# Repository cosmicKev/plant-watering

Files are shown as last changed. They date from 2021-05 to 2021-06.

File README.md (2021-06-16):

# Self Watering Plant

To keep your veggies alive that came alive from the [OfferZen] (http://offerzen.com/nl/make) workshop

# Features
  - ESP32 (Wifi / Bluetooth)
  - Flashing is done with a single USB-TypeC
  - Power in:
    - USB at 5V @ 2A max
  - Outputs
    - 2x waterpumps individually with shared power supply of either +5V or +12V
    - 2x USB 5V led strips individually controlled.
  - Sensors:
    - 2x external moisture sensors
    - 1x on board light sensor
    - 1x on board humidity & temperature sesor
    - 1x user custom sensor (till 3.3V

# MCAD - Mechanical CAD
## Pot pipe clips

## Electronics Enclosure

# ECAD - Electronics CAD

# Firmware

# Version

# Authors
Kevin Pinto

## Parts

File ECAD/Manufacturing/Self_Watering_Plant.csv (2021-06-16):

Comment | Designator | Footprint | LCSC Part #
10nF Unpolarized capacitor, small symbol | C1,C3,C11,C13 | C_0603_1608Metric
10uF Unpolarized capacitor, small symbol | C2 | C_0603_1608Metric
0.1uF Unpolarized capacitor, small symbol | C4,C5,C7,C8,C15,C16,C17 | C_0603_1608Metric
1uF Unpolarized capacitor, small symbol | C6,C12,C14 | C_0603_1608Metric
NCD0603R1 Light emitting diode | D1,D2,D4,D5,D7,D8 | LED_0603_1608Metric
RS3ABG Diode | D3,D6 | D_SMB
Polyfuse_Small Resettable fuse, polymeric positive temperature coefficient, small symbol | F1 | Fuse_1812_4532Metric
Conn_01x02 Generic connector, single row, 01x02, script generated (kicad-library-utils/schlib/autogen/connector/) | J1,J2 | TB001-500-02BE
USB_A USB Type A connector | J3,J6 | USB_A_Molex_67643_Horizontal
Conn_01x02 Generic connector, single row, 01x02, script generated (kicad-library-utils/schlib/autogen/connector/) | J7,J8 | JST_XH_S2B-XH-A_1x02_P2.50mm_Horizontal
Conn_01x03 Generic connector, single row, 01x03, script generated (kicad-library-utils/schlib/autogen/connector/) | J9 | JST_XH_S3B-XH-A_1x03_P2.50mm_Horizontal
C-31-M-12 USB 2.0-only Type-C Plug connector | P1 | USB_C_Receptacle_HRO_TYPE-C-31-M-12
BC817 0.8A Ic, 45V Vce, NPN Transistor, SOT-23 | Q1,Q2 | SOT-23
TEPT4400 Ambient Light Sensor, NPN Epitaxial Planar Phototransistor, T-1 | Q9 | LED_D3.0mm_Clear
10K Resistor, small symbol | R1,R4,R8,R9,R11,R14 | R_0603_1608Metric
5.1K Resistor, small symbol | R2,R5,R13,R15 | R_0603_1608Metric
1K Resistor, small symbol | R3,R6,R7,R12,R17,R18 | R_0603_1608Metric
0 Resistor, small symbol | R10 | R_0603_1608Metric
SW_Push Push button switch, generic, two pins | SW1 | SW_PUSH_6mm_H4.3mm
ESP32-WROOM-32 RF Module, ESP32-D0WDQ6 SoC, Wi-Fi 802.11b/g/n, Bluetooth, BLE, 32-bit, 2.7-3.6V, onboard antenna, SMD | U1 | ESP32-WROOM-32
NCE3018AS VDS =30V,ID =18A RDS(ON) < 7mΩ @ VGS=10V RDS(ON) < 10mΩ @ VGS=4.5V | U2,U9,U13,U14 | SO-8_3.9x4.9mm_P1.27mm
CH340C USB serial converter, UART, SOIC-16 | U3 | SOIC-16_3.9x9.9mm_P1.27mm
AHT20 | U4 | SOIC-6
NC7SB3157P6X Single SPDT Low-Voltage Analog Switch or 2:1 Multiplexer/De-Multiplexer Bus Switch, 10Ohm Ron, SC-70-6 | U5,U6,U7 | SOT-363_SC-70-6
BCT2028 | U11 | SOT-23-5

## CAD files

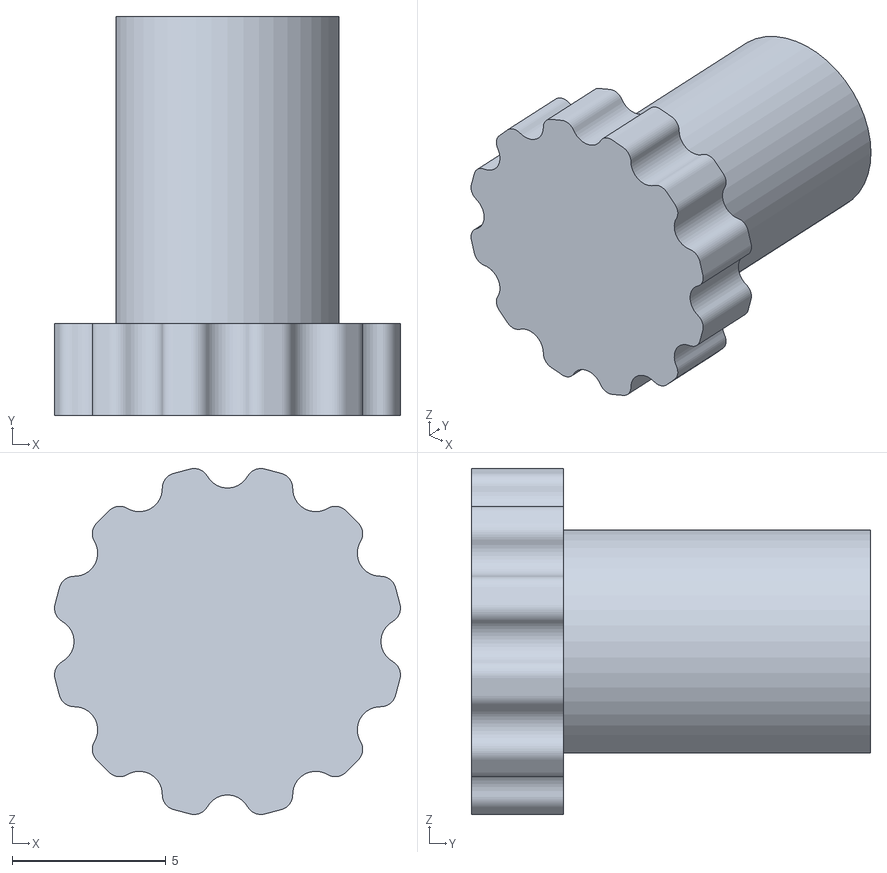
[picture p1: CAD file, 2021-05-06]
MCAD/PipeCork.STL
11.3 x 13.0 x 11.3

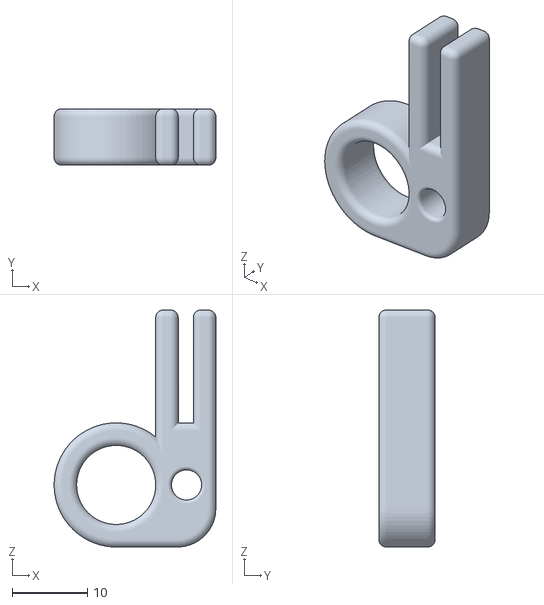
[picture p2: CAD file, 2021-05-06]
MCAD/PipeClip.STL
21.5 x 7.50 x 31.5

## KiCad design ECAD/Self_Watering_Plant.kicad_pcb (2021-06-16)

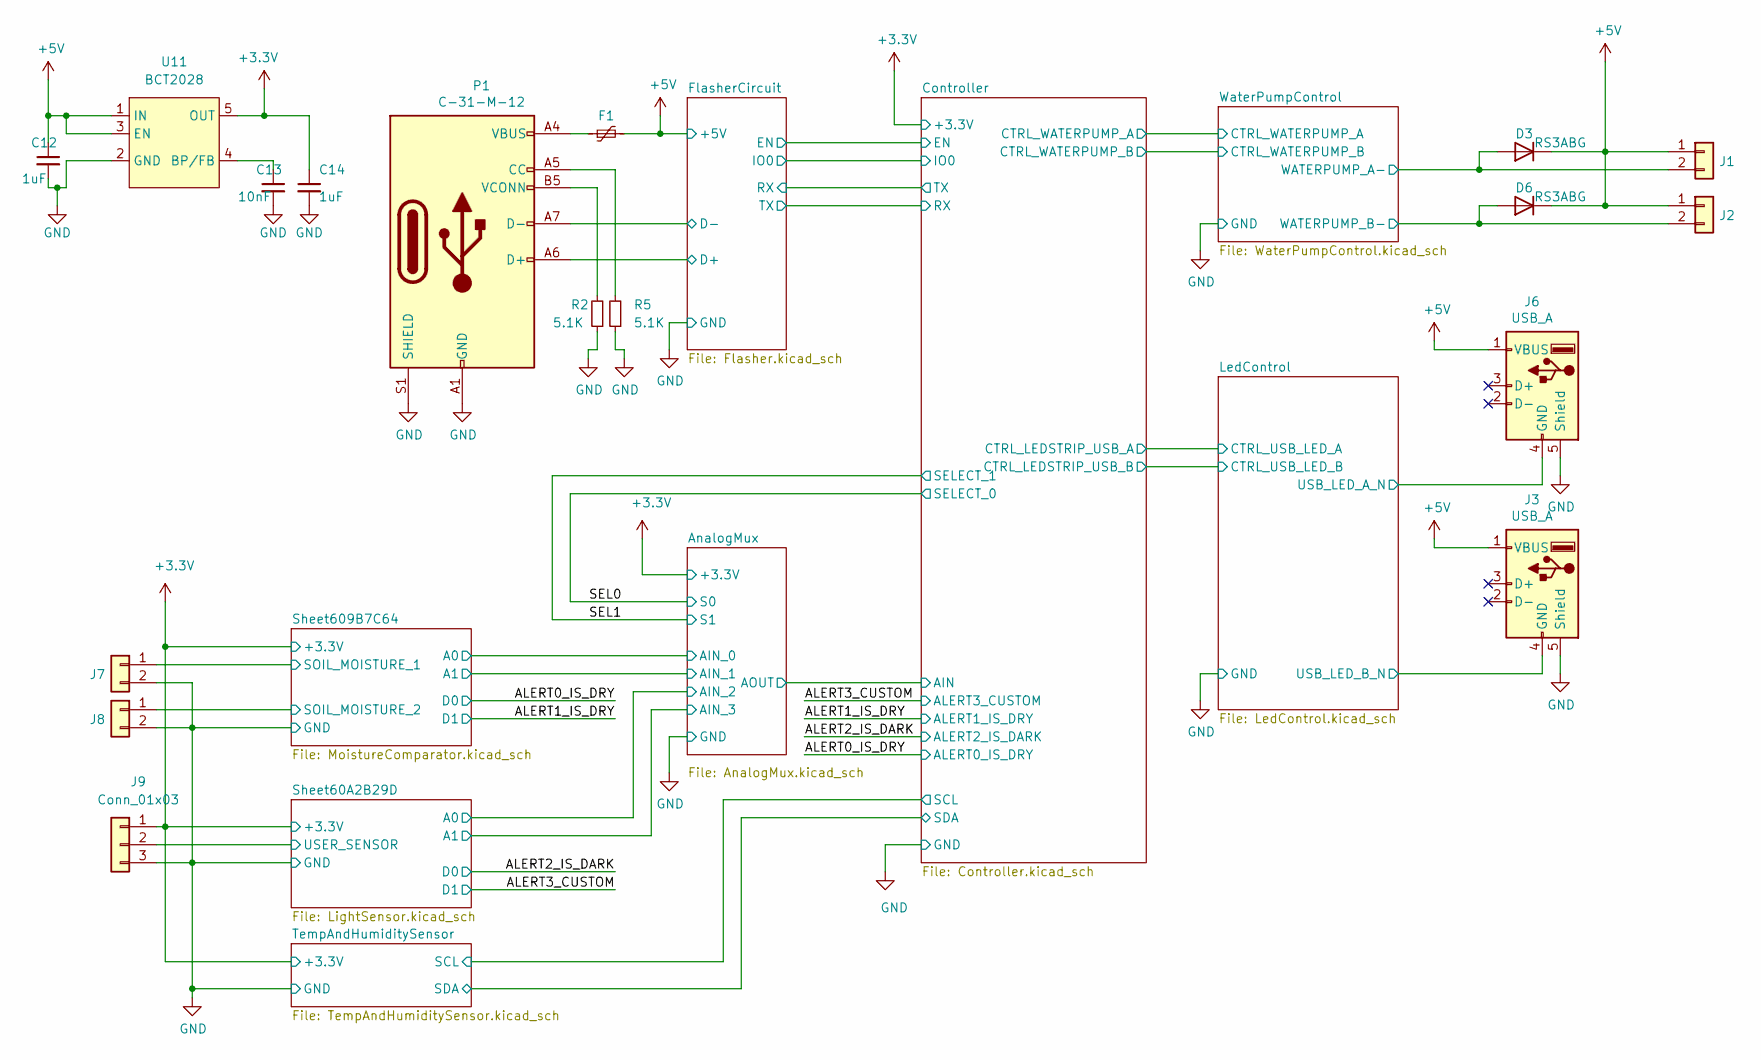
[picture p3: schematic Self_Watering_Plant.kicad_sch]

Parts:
C12, C14: 1uF; C_0603_1608Metric
C13: 10nF; C_0603_1608Metric
D3, D6: RS3ABG; D_SMB
F1: Polyfuse_Small; Fuse_1812_4532Metric
J1, J2: Conn_01x02; TB001-500-02BE
J3, J6: USB_A; USB_A_Molex_67643_Horizontal
J7, J8: Conn_01x02; JST_XH_S2B-XH-A_1x02_P2.50mm_Horizontal
J9: Conn_01x03; JST_XH_S3B-XH-A_1x03_P2.50mm_Horizontal
P1: C-31-M-12; USB_C_Receptacle_HRO_TYPE-C-31-M-12
R2, R5: 5.1K; R_0603_1608Metric
U11: BCT2028; SOT-23-5

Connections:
+3V3: C14.1, J9.1, U11.5 (OUT); also elsewhere on the board
+5V: C12.1, D3.1 (K), D6.1 (K), F1.2, J1.1, J2.1, J3.1 (VBUS), J6.1 (VBUS), U11.1 (IN), U11.3 (EN); also elsewhere on the board
/AnalogMux/AIN_0: J8.1; also elsewhere on the board
/AnalogMux/AIN_1: J7.1; also elsewhere on the board
/AnalogMux/AIN_2: J9.2; also elsewhere on the board
/FlasherCircuit/D+: P1.A6 (D+); also elsewhere on the board
/FlasherCircuit/D-: P1.A7 (D-); also elsewhere on the board
/LedControl/USB_LED_A_N: J6.4 (GND); also elsewhere on the board
/LedControl/USB_LED_B_N: J3.4 (GND); also elsewhere on the board
/WaterPumpControl/WATERPUMP_A-: D3.2 (A), J1.2; also elsewhere on the board
/WaterPumpControl/WATERPUMP_B-: D6.2 (A), J2.2; also elsewhere on the board
GND: C12.2, C13.2, C14.2, J3.5 (Shield), J6.5 (Shield), J7.2, J8.2, J9.3, P1.A1 (GND), P1.A12 (GND), P1.B1 (GND), P1.B12 (GND), P1.S1 (SHIELD), R2.1, R5.1, U11.2 (GND); also elsewhere on the board
unnamed: C13.1, U11.4 (BP/FB)
unnamed: F1.1, P1.A4 (VBUS), P1.A9 (VBUS), P1.B4 (VBUS), P1.B9 (VBUS)
unnamed: P1.A5 (CC), R5.2
unnamed: P1.B5 (VCONN), R2.2

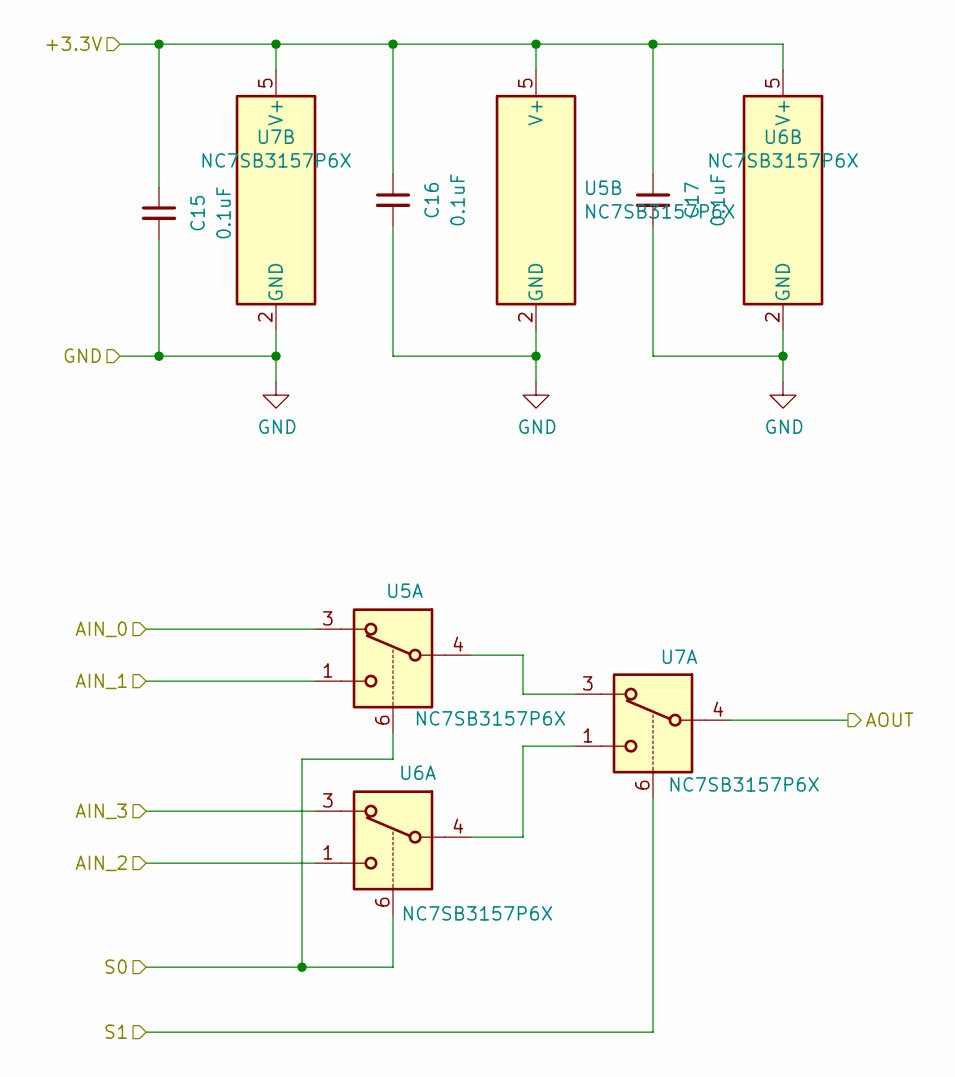
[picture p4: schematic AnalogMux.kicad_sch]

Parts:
C15, C16, C17: 0.1uF; C_0603_1608Metric
U5, U6, U7: NC7SB3157P6X; SOT-363_SC-70-6

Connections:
+3V3: C15.1, C16.1, C17.1, U5.5 (V+), U6.5 (V+), U7.5 (V+); also elsewhere on the board
/AnalogMux/AIN_0: U5.3; also elsewhere on the board
/AnalogMux/AIN_1: U5.1; also elsewhere on the board
/AnalogMux/AIN_2: U6.1; also elsewhere on the board
/AnalogMux/AIN_3: U6.3; also elsewhere on the board
/AnalogMux/AOUT: U7.4; also elsewhere on the board
/SEL0: U5.6, U6.6; also elsewhere on the board
/SEL1: U7.6; also elsewhere on the board
GND: C15.2, C16.2, C17.2, U5.2 (GND), U6.2 (GND), U7.2 (GND); also elsewhere on the board
unnamed: U5.4, U7.3
unnamed: U6.4, U7.1

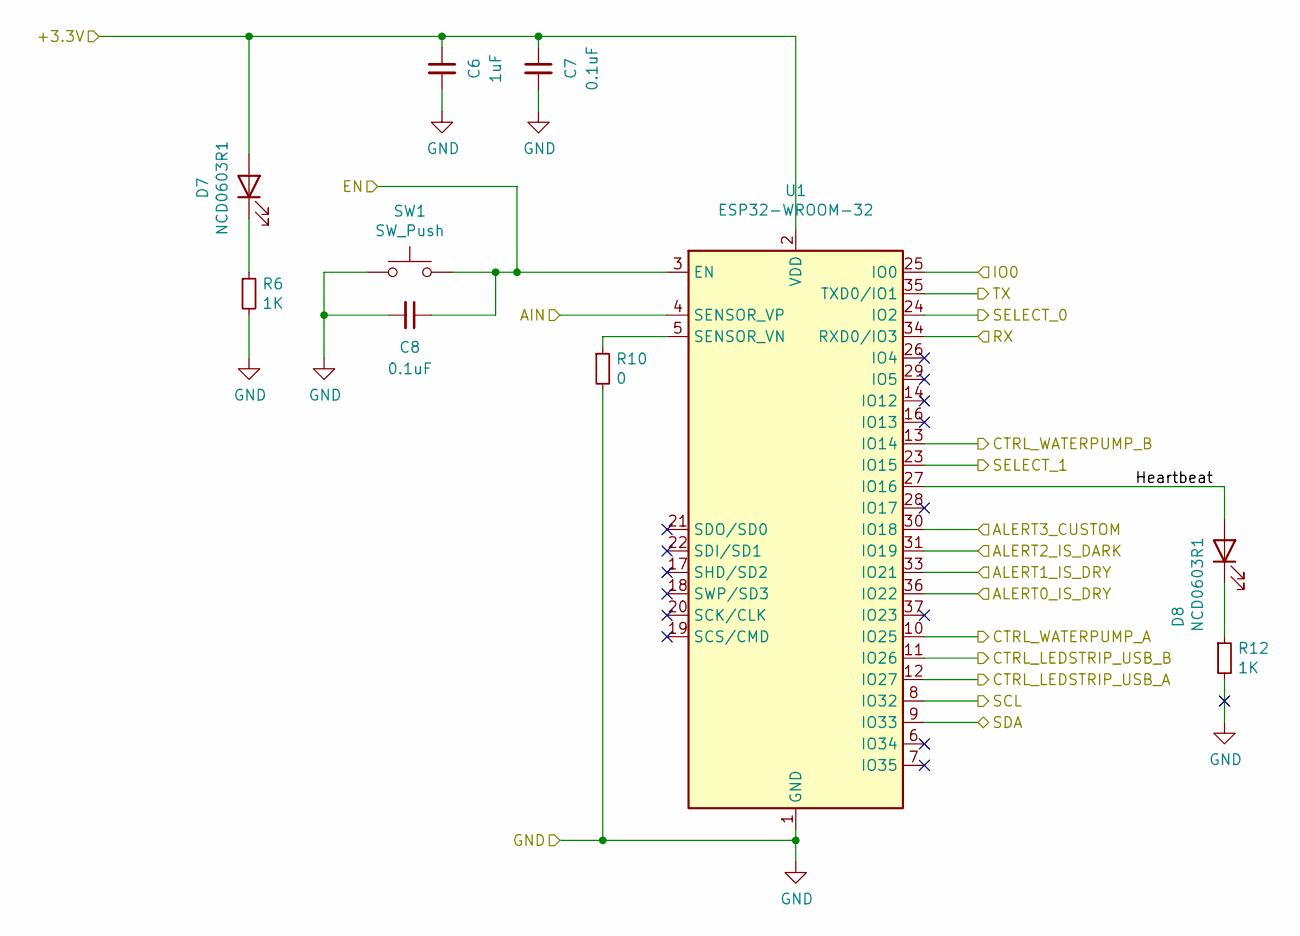
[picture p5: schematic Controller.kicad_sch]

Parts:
C6: 1uF; C_0603_1608Metric
C7, C8: 0.1uF; C_0603_1608Metric
D7, D8: NCD0603R1; LED_0603_1608Metric
R6, R12: 1K; R_0603_1608Metric
R10: 0; R_0603_1608Metric
SW1: SW_Push; SW_PUSH_6mm_H4.3mm
U1: ESP32-WROOM-32

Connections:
+3V3: C6.1, C7.1, D7.2 (A), U1.2 (VDD); also elsewhere on the board
/ALERT0_IS_DRY: U1.36 (IO22); also elsewhere on the board
/ALERT1_IS_DRY: U1.33 (IO21); also elsewhere on the board
/ALERT2_IS_DARK: U1.31 (IO19); also elsewhere on the board
/ALERT3_CUSTOM: U1.30 (IO18); also elsewhere on the board
/AnalogMux/AOUT: U1.4 (SENSOR_VP); also elsewhere on the board
/Controller/CTRL_LEDSTRIP_USB_A: U1.12 (IO27); also elsewhere on the board
/Controller/CTRL_LEDSTRIP_USB_B: U1.11 (IO26); also elsewhere on the board
/Controller/CTRL_WATERPUMP_A: U1.10 (IO25); also elsewhere on the board
/Controller/CTRL_WATERPUMP_B: U1.13 (IO14); also elsewhere on the board
/Controller/EN: C8.1, SW1.2, U1.3 (EN); also elsewhere on the board
/Controller/Heartbeat: D8.2 (A), U1.27 (IO16)
/Controller/IO0: U1.25 (IO0); also elsewhere on the board
/Controller/RX: U1.34 (RXD0/IO3); also elsewhere on the board
/Controller/SCL: U1.8 (IO32); also elsewhere on the board
/Controller/SDA: U1.9 (IO33); also elsewhere on the board
/Controller/TX: U1.35 (TXD0/IO1); also elsewhere on the board
/SEL0: U1.24 (IO2); also elsewhere on the board
/SEL1: U1.23 (IO15); also elsewhere on the board
GND: C6.2, C7.2, C8.2, R6.2, R10.2, R12.2, SW1.1, U1.1 (GND), U1.15 (GND), U1.38 (GND), U1.39 (GND); also elsewhere on the board
unnamed: D7.1 (K), R6.1
unnamed: D8.1 (K), R12.1
unnamed: R10.1, U1.5 (SENSOR_VN)

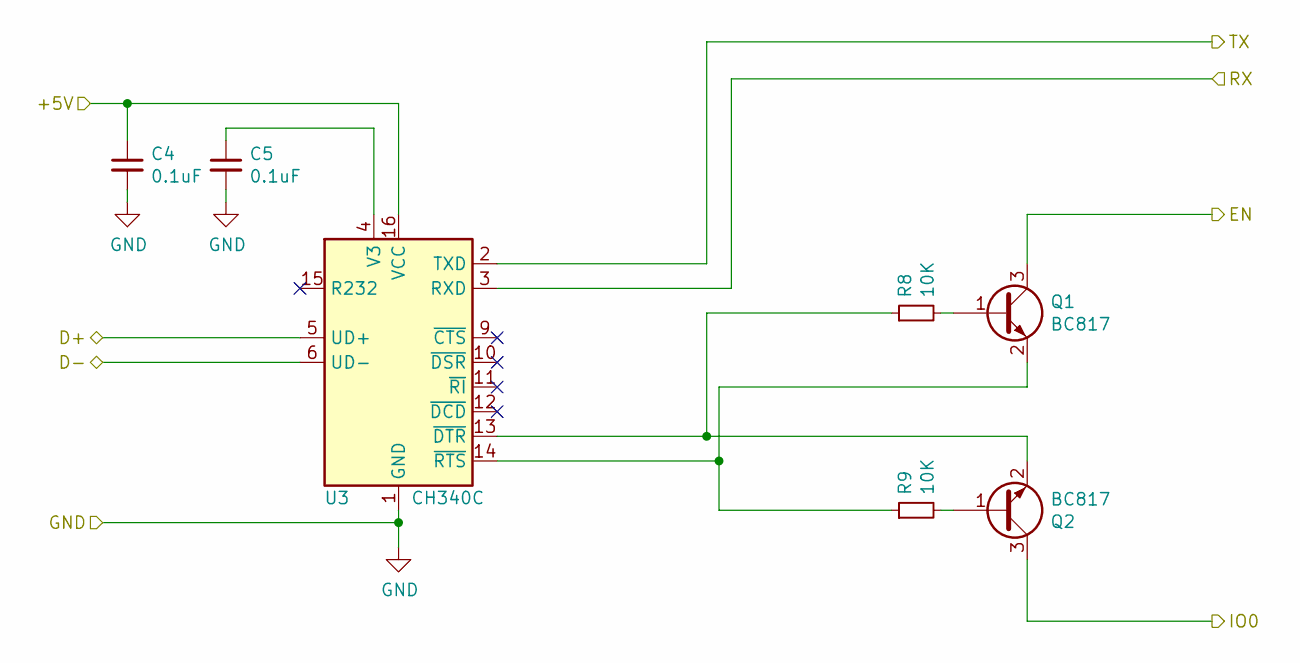
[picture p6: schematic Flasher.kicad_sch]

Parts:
C4, C5: 0.1uF; C_0603_1608Metric
Q1, Q2: BC817; SOT-23
R8, R9: 10K; R_0603_1608Metric
U3: CH340C; SOIC-16_3.9x9.9mm_P1.27mm

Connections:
+5V: C4.1, U3.16 (VCC); also elsewhere on the board
/Controller/EN: Q1.3 (C); also elsewhere on the board
/Controller/IO0: Q2.3 (C); also elsewhere on the board
/Controller/RX: U3.2 (TXD); also elsewhere on the board
/Controller/TX: U3.3 (RXD); also elsewhere on the board
/FlasherCircuit/D+: U3.5 (UD+); also elsewhere on the board
/FlasherCircuit/D-: U3.6 (UD-); also elsewhere on the board
GND: C4.2, C5.2, U3.1 (GND); also elsewhere on the board
unnamed: C5.1, U3.4 (V3)
unnamed: Q1.1 (B), R8.2
unnamed: Q1.2 (E), R9.1, U3.14 (~RTS)
unnamed: Q2.1 (B), R9.2
unnamed: Q2.2 (E), R8.1, U3.13 (~DTR)

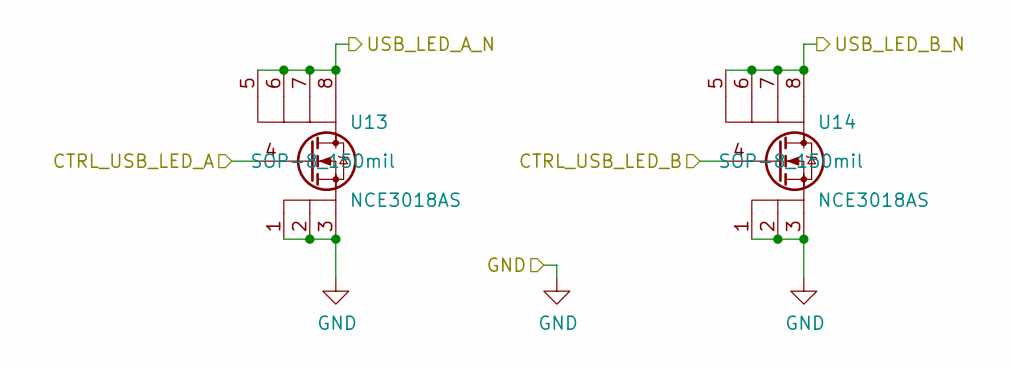
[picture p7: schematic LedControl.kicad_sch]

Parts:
U13, U14: NCE3018AS; SO-8_3.9x4.9mm_P1.27mm

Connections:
/Controller/CTRL_LEDSTRIP_USB_A: U13.4; also elsewhere on the board
/Controller/CTRL_LEDSTRIP_USB_B: U14.4; also elsewhere on the board
/LedControl/USB_LED_A_N: U13.5, U13.6, U13.7, U13.8; also elsewhere on the board
/LedControl/USB_LED_B_N: U14.5, U14.6, U14.7, U14.8; also elsewhere on the board
GND: U13.1, U13.2, U13.3, U14.1, U14.2, U14.3; also elsewhere on the board

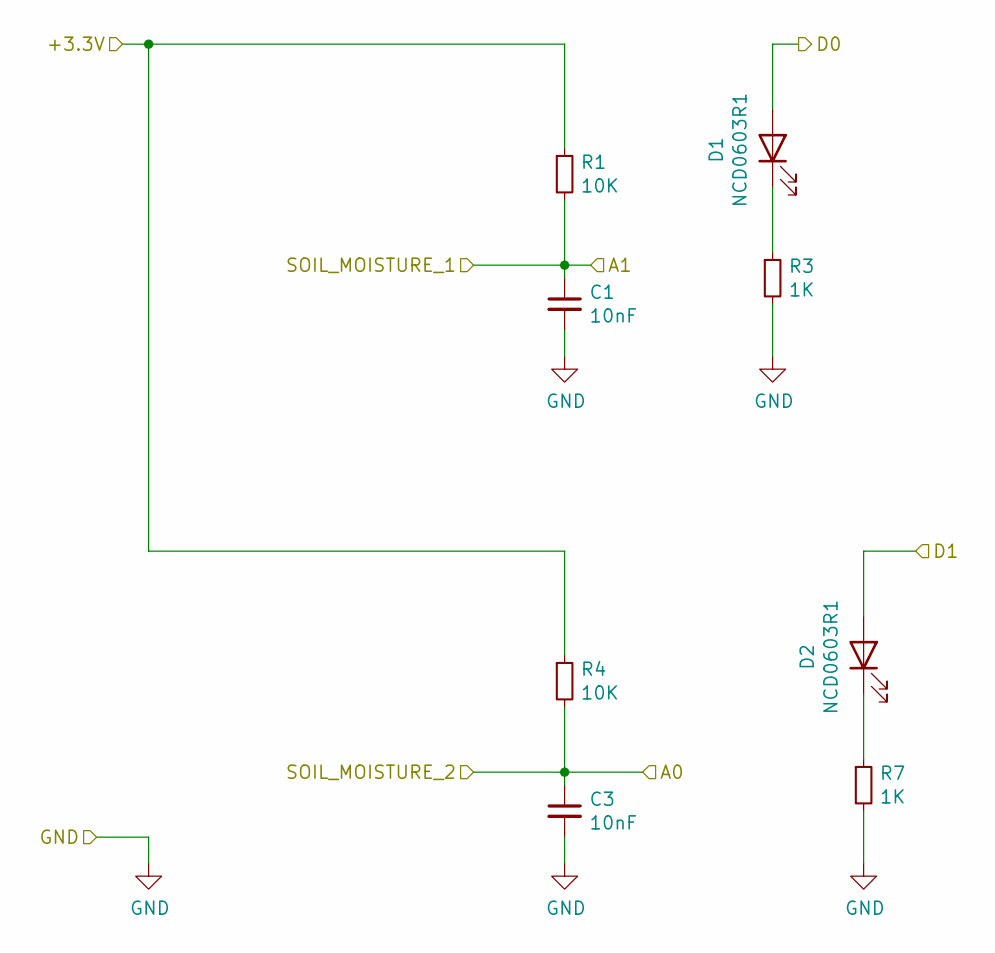
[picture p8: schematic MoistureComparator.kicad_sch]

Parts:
C1, C3: 10nF; C_0603_1608Metric
D1, D2: NCD0603R1; LED_0603_1608Metric
R1, R4: 10K; R_0603_1608Metric
R3, R7: 1K; R_0603_1608Metric

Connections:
+3V3: R1.1, R4.1; also elsewhere on the board
/ALERT0_IS_DRY: D1.2 (A); also elsewhere on the board
/ALERT1_IS_DRY: D2.2 (A); also elsewhere on the board
/AnalogMux/AIN_0: C3.1, R4.2; also elsewhere on the board
/AnalogMux/AIN_1: C1.1, R1.2; also elsewhere on the board
GND: C1.2, C3.2, R3.2, R7.2; also elsewhere on the board
unnamed: D1.1 (K), R3.1
unnamed: D2.1 (K), R7.1

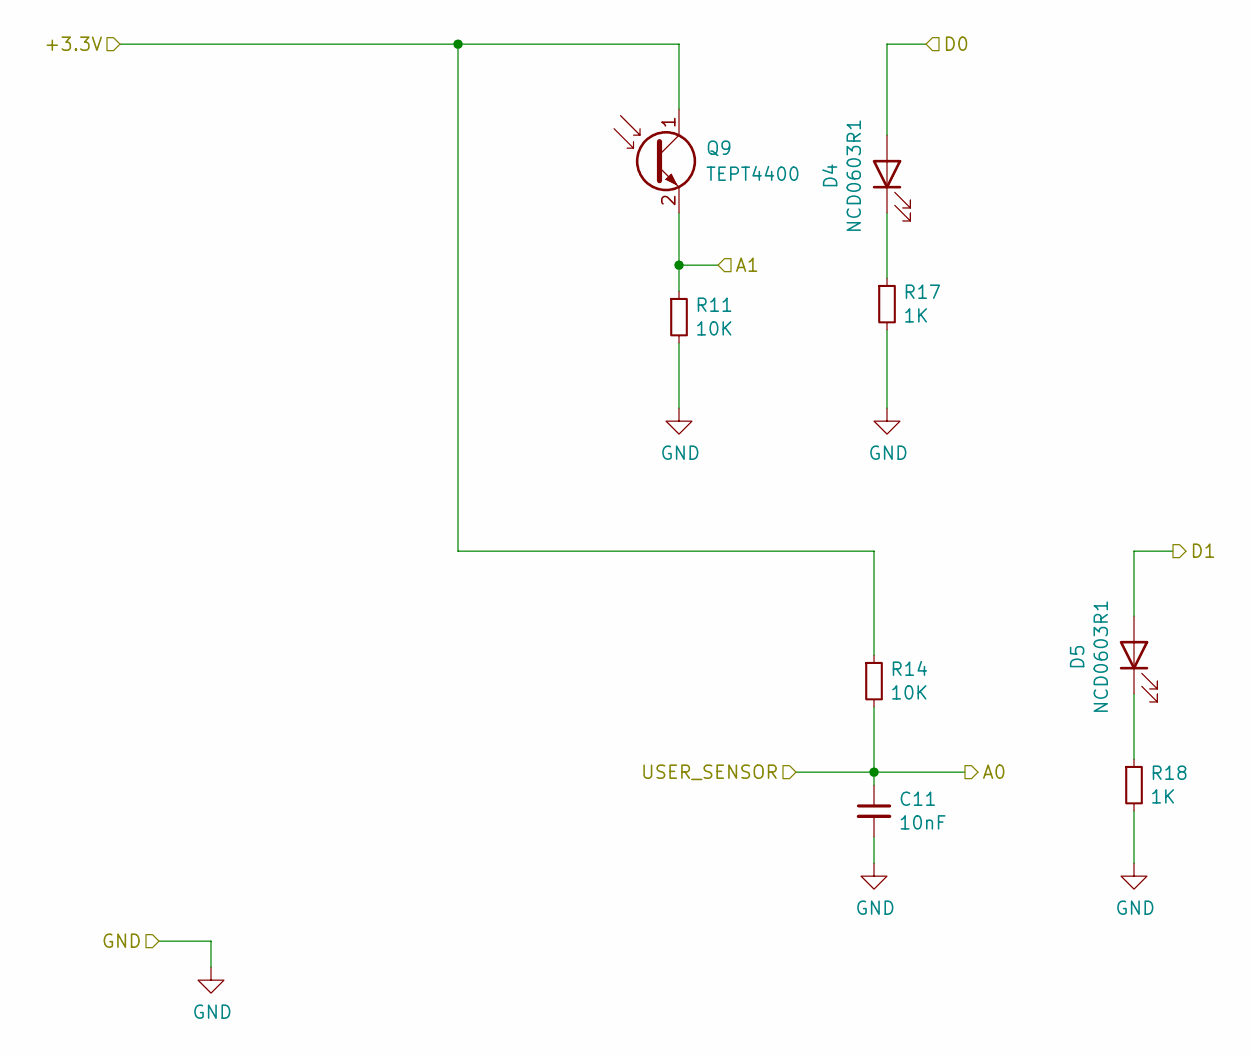
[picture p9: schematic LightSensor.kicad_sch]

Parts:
C11: 10nF; C_0603_1608Metric
D4, D5: NCD0603R1; LED_0603_1608Metric
Q9: TEPT4400; LED_D3.0mm_Clear
R11, R14: 10K; R_0603_1608Metric
R17, R18: 1K; R_0603_1608Metric

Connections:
+3V3: Q9.1 (C), R14.1; also elsewhere on the board
/ALERT2_IS_DARK: D4.2 (A); also elsewhere on the board
/ALERT3_CUSTOM: D5.2 (A); also elsewhere on the board
/AnalogMux/AIN_2: C11.1, R14.2; also elsewhere on the board
/AnalogMux/AIN_3: Q9.2 (E), R11.1; also elsewhere on the board
GND: C11.2, R11.2, R17.2, R18.2; also elsewhere on the board
unnamed: D4.1 (K), R17.1
unnamed: D5.1 (K), R18.1

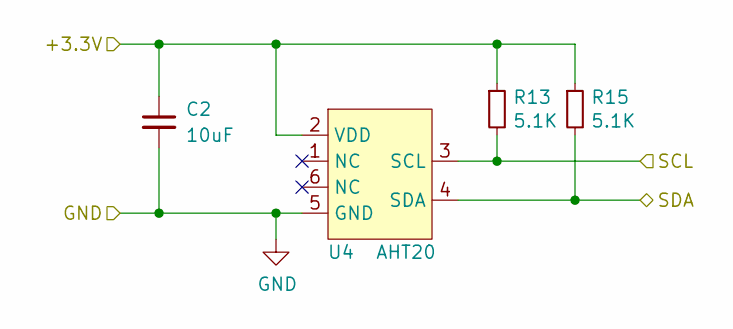
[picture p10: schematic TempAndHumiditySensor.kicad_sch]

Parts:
C2: 10uF; C_0603_1608Metric
R13, R15: 5.1K; R_0603_1608Metric
U4: AHT20; SOIC-6

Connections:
+3V3: C2.1, R13.1, R15.1, U4.2 (VDD); also elsewhere on the board
/Controller/SCL: R13.2, U4.3 (SCL); also elsewhere on the board
/Controller/SDA: R15.2, U4.4 (SDA); also elsewhere on the board
GND: C2.2, U4.5 (GND); also elsewhere on the board

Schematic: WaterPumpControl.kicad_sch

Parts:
U2, U9: NCE3018AS; SO-8_3.9x4.9mm_P1.27mm

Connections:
/Controller/CTRL_WATERPUMP_A: U2.4; also elsewhere on the board
/Controller/CTRL_WATERPUMP_B: U9.4; also elsewhere on the board
/WaterPumpControl/WATERPUMP_A-: U2.5, U2.6, U2.7, U2.8; also elsewhere on the board
/WaterPumpControl/WATERPUMP_B-: U9.5, U9.6, U9.7, U9.8; also elsewhere on the board
GND: U2.1, U2.2, U2.3, U9.1, U9.2, U9.3; also elsewhere on the board

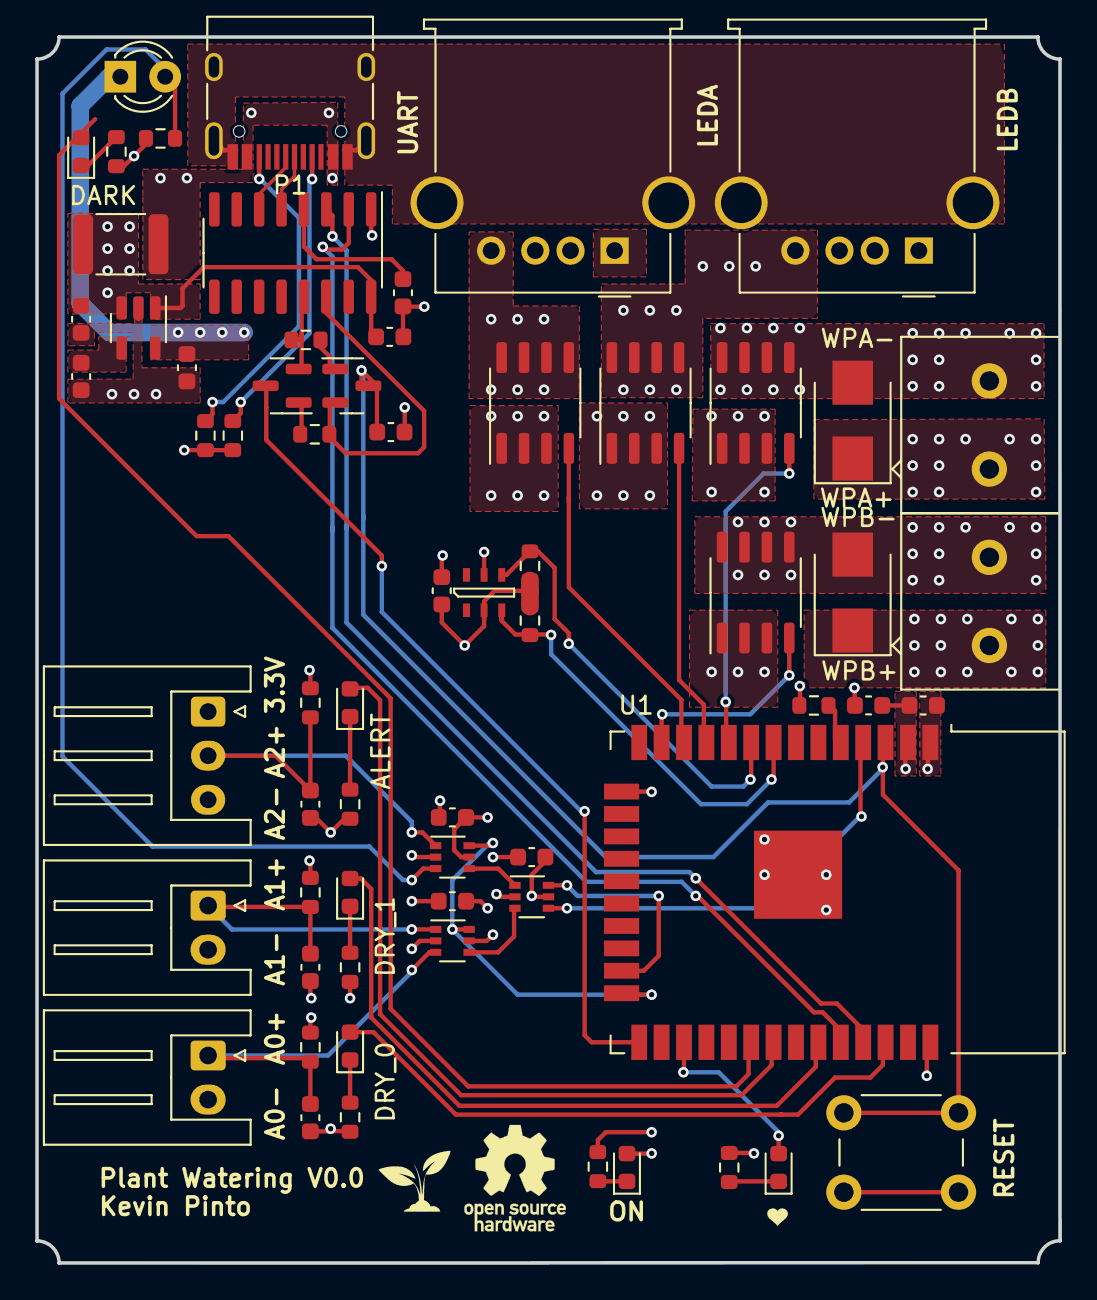
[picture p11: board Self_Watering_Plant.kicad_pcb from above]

Board: 4 copper layers, 58.0 x 69.5 mm, 64 parts (0 on the bottom side), 49 nets.

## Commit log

2021-05-06 adding 3d printed files of fixtures for the plant pot
    [PipeClip.STL, PipeCork.STL]
2021-05-07 making a small pcb that contains everything we learn from the workshop with sensors and other functionality
    [AnalogMux.sch, Controller.sch, Flasher.sch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]
2021-05-07 porting project to kicad 5.99, fixing some error in schematics. Getting ready to lay down the layout and order in jlcpcb
    [AnalogMux.kicad_sch, Controller.kicad_sch, Flasher.kicad_sch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]
2021-05-09 pcb layout has started, still ned to make 5V to 3.3V power supply, add dip switch do individually control input power of each switch, 5V or 12V
    [AnalogMux.kicad_sch, LightSensor.kicad_sch, MoistureComparator.kicad_sch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]
2021-05-16 finishing up pcb, only billonly bill of materials need to be done to be compatible with lc from jlcpcb
    [AnalogMux.kicad_sch, Controller.kicad_sch, Flasher.kicad_sch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]
2021-05-16 BOM fixed, ready to order
    [AnalogMux.kicad_sch, Controller.kicad_sch, Flasher.kicad_sch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]
2021-05-16 found quite some errors after my review, fixed them before purchase a sample of 5
    [Self_Watering_Plant-B_Cu.gbr, Self_Watering_Plant-B_Fab.gbr, Self_Watering_Plant-B_Mask.gbr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]
2021-06-16 adding production and step files
    [AnalogMux.kicad_sch, Controller.kicad_sch, Flasher.kicad_sch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]
